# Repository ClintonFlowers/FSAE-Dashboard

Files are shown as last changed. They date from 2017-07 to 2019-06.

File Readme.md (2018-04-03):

# KSU Motorsports Dashboard & Data Logger

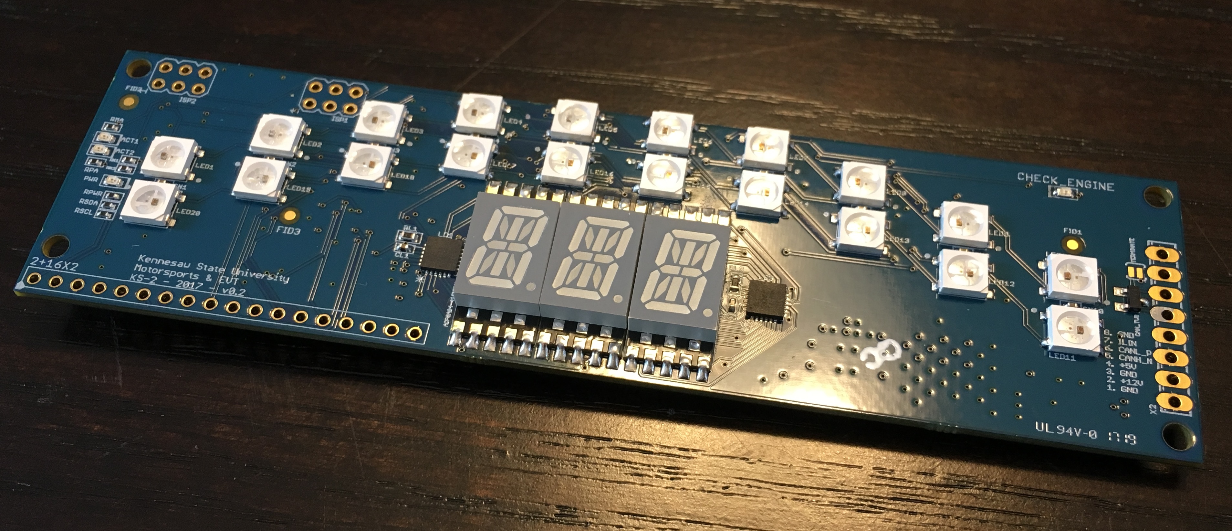
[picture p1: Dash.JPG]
KS-2 Dashboard


This is a custom dashboard / shift-light module created for the Kennesaw State University Motorsports student-built race car, the KS-2.
In a 5" x 1.25" x 0.5" footprint, it has:

* 20 individually-addressable RGB LED's (Neopixels)
* 3 14-segment alphanumeric LED elements for string output via scrolling text
* CAN bus communication with solderable termination jumper
* Onboard 12V to 5V switching converter plus overvoltage, transient, overcurrent, and reverse-voltage protection (i.e., Partially Student Resistant)
* A 9-DOF (accelerometer/gyro/magnetometer) inertial measurement unit with integrated sensor fusion
* A battery-backed Realtime Clock
* A Micro SD Card slot
* A 5-way Tactile Switch/Joystick
* Expansion capability via a 0.1" header at the bottom left, designed for a 16x2 character matrix or any I2C device

It's based on a combination of a Atmega328P (Arduino Uno) and a Atmega2560 (Arduino Mega) to ensure team members can program it into the future.

I've included a PDF to view the schematic without EagleCAD, and the models (STL/SLDPRT) of the enclosure pieces. The version 1 faceplate and backplate were designed for Formlabs clear resin, as the backplate's integrated cable-tie strain-relief loops may break more easily on FDM prints (due to Z-axis layer adhesion). Newer designs (version 2+) use a thin waterjet polycarbonate faceplate for simplicity.

Feel free to contact me with any questions,

Clinton Flowers

clintonflowers222@gmail.com

   Copyright 2017 Clinton Flowers

   Licensed under the Apache License, Version 2.0 (the "License");
   you may not use this file except in compliance with the License.
   You may obtain a copy of the License at

       http://www.apache.org/licenses/LICENSE-2.0

   Unless required by applicable law or agreed to in writing, software
   distributed under the License is distributed on an "AS IS" BASIS,
   WITHOUT WARRANTIES OR CONDITIONS OF ANY KIND, either express or implied.
   See the License for the specific language governing permissions and
   limitations under the License.

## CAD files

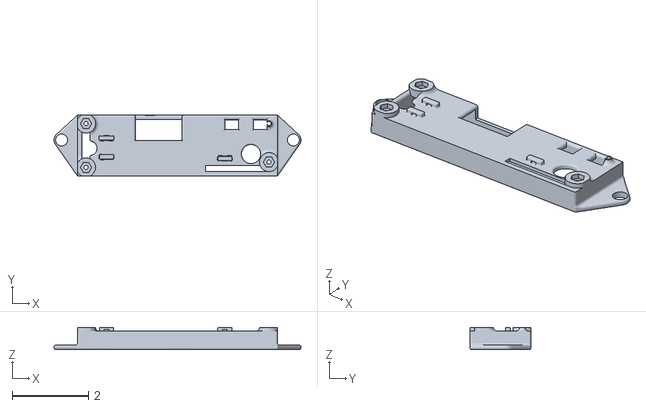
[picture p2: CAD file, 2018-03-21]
Enclosure/Dash v0.2 Backplate Version 2.STL
6.48 x 1.60 x 0.587

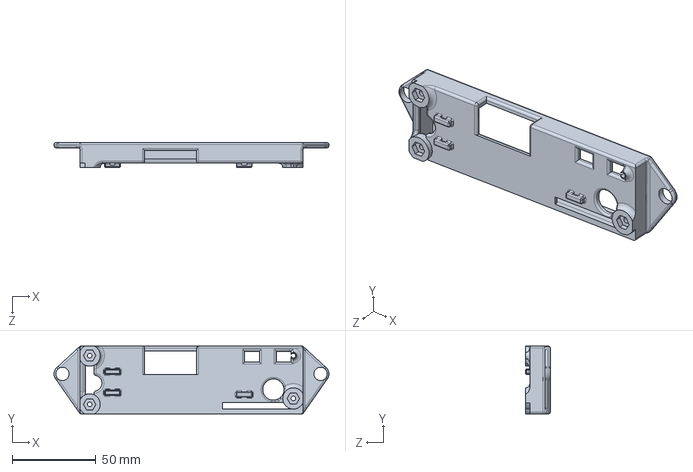
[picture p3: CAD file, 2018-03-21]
Enclosure/Dash Faceplate Version 2.SLDPRT
164.6 x 40.6 x 14.9 mm

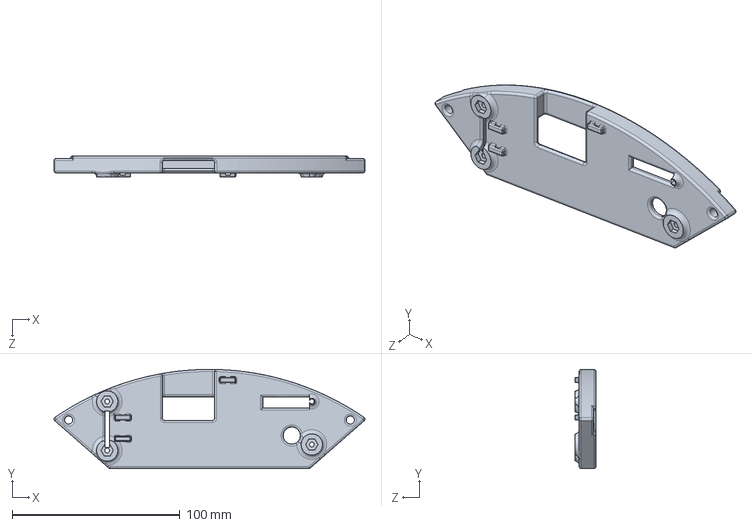
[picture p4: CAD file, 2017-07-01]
Enclosure/Dash Backplate.SLDPRT
185.3 x 59.1 x 12.7 mm

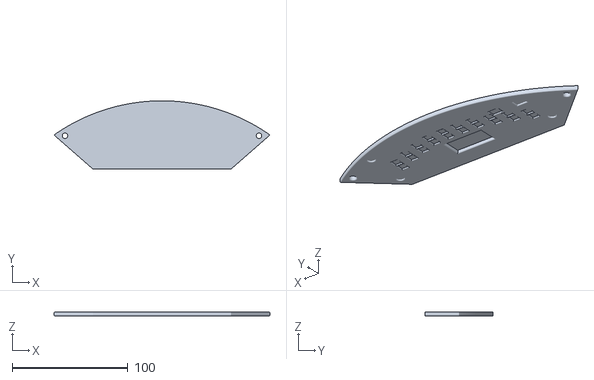
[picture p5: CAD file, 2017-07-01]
Enclosure/Dash v0.2 Faceplate - Formlabs Clear Resin.STL
186.9 x 59.1 x 3.17

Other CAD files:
Enclosure/Dash v0.2 Backplate - Formlabs Clear Resin.STL
Enclosure/Dash Faceplate.SLDPRT

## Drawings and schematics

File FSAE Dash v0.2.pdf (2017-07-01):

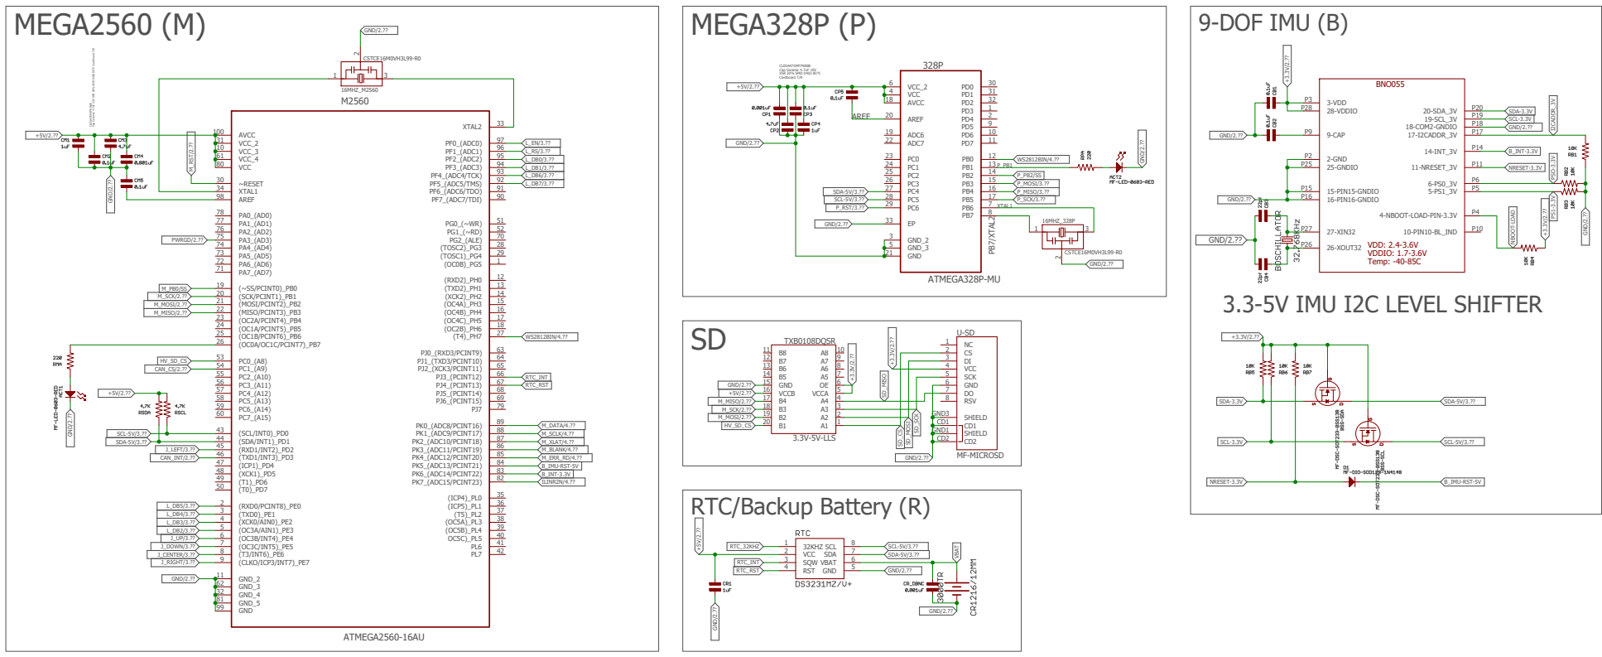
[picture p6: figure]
CL05A475MP7NRB8; 9-DOF IMU (B); 3.3-5V IMU I2C LEVEL SHIFTER; RTC/Backup Battery (R); ATMEGA328P-MU; CSTCE16M0VH3L99-R0; ATMEGA2560-16AU; MF-MICROSD; TXB0108DQSR; MEGA2560 (M); MEGA328P (P); VCC_2 6 VCC 4 AVCC 18; AREF 20; ADC6 19 ADC7 22; GND_2 3 GND_3 5 GND 21; 16MHZ_328P; AVCC 100 VCC_2 31 VCC_3 10 VCC_4 61 VCC 80; ~RESET 30 XTAL1 34 AREF 98; (~SS/PCINT0)_PB0 19 (SCK/PCINT1)_PB1 20 (MOSI/PCINT2)_PB2 21 (MISO/PCINT3)_PB3 22 (OC2A/PCINT4)_PB4 23 (OC1A/PCINT5)_PB5 24 (OC1B/PCINT6)_PB6 25 (OC0A/OC1C/PCINT7)_PB7 26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

Cap Ceramic 4.7uF 10V X5R 20% SMD 0402 85°C Cardboard T/R CL05A475MP7NRB8 Cap Ceramic 4.7uF 10V X5R 20% SMD 0402 85°C Cardboard T/R

# Key: *P* | P_* = ATMega328P *M* | M_* = ATMega2560 C* = Capacitor R* = Resistor (plus arbitrary variants like CP* meaning a capacitor for 328P) *N* | N_* = Neopixel (WS2812B's)

# References: http://www.14core.com/wp-content/uploads/2015/06/ATMEGA-2560-Pin-Out-Diagram.png

# CONTROL

# NOTES:

The original boards were manufactured using MacroFab's standard 4-layer turnkey process.
If needed, my own library has been included.

Objects beginning with "MF" are from the MacroFab Eagle library, available on Github, along with the relevant DRC. MacroFab has a relatively long lead time (~1mo) and occasionally makes mistakes,
so budget in some ChipQuik and don't procrastinate with orders.
MacroFab's system pulls model numbers from the Eagle "value" field,
so if you're not sure what something here is, see if there's not something in it.

Special thanks to SparkFun and Adafruit OSHW designs, on which parts of this are based.

# Also FYI: WS2812B's (the LED's) have an equivalent Moisture Sensitivity Level 6!

Using them in a reflow oven without using desiccants and baking them before use will lead to cracked epoxy lenses! Resoldering them by hand was not fun.
(The next versions will use the newer variants with redundant data lines as an extra precaution.)

# Clinton Flowers, 2017-7-01 clintonflowers222@gmail.com Kennesaw State University Motorsports

A1 1 A2 2 A3 3 A4 4 VCCA 5 OE 6 A5 7 A6 8 A7 9 A8 10 B8 11 B7 12 B6 13 B5 14 GND 15 VCCB 16 B4 17 B3 18 B2 19 B1 20

5V->3.3V

# CAN/POWER

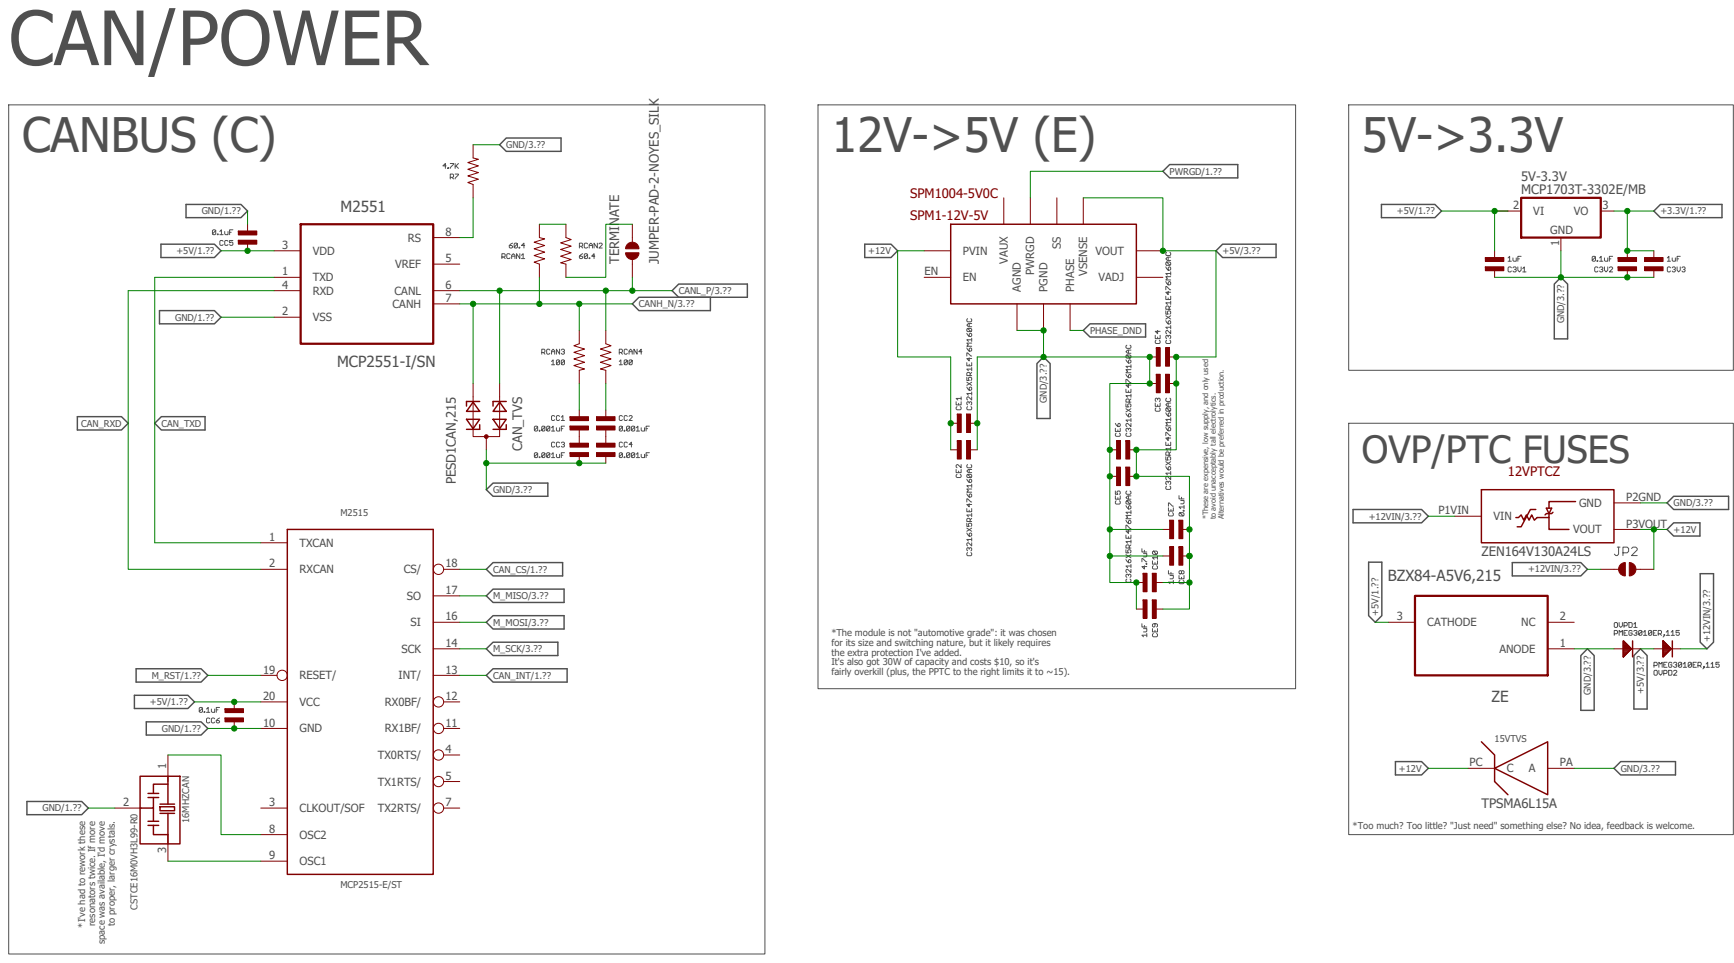
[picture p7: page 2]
TPSMA6L15A; ZEN164V130A24LS; MCP2515-E/ST; MCP2551-I/SN; CSTCE16M0VH3L99-R0; PESD1CAN,215; MCP1703T-3302E/MB; BZX84-A5V6,215; RESET/ 19; SCK; INT/; TX0RTS/; VCC 20; GND 10; TXCAN 1; RXCAN 2; OSC1 9; OSC2 8; CLKOUT/SOF 3; TX1RTS/; TX2RTS/; VDD 3; TXD 1; VSS 2; RXD 4; VREF; CANL; CANH; 16MHZCAN; CAN_TVS; PVIN; VAUX; PWRGD; PGND; PHASE; GND; ANODE; 2 CATHODE 3; VIN P1VIN; P2GND; VOUT; P3VOUT; TERMINATE; 15VTVS; M_MOSI/3.??; CANH_N/3.??; GND/1.??; GND/3.??; CAN_RXD; CAN_TXD; CAN_INT/1.??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

JUMPER-PAD-2-NOYES_SILK CANBUS (C) 12V->5V (E)

VSENSE VOUT VADJ AGND

*These are expensive, low supply, and only used

Alternatives would be preferred in production.

to avoid unacceptably tall electrolytics.

OVP/PTC FUSES

*The module is not "automotive grade": it was chosen
for its size and switching nature, but it likely requires
the extra protection I've added.
It's also got 30W of capacity and costs $10, so it's
fairly overkill (plus, the PPTC to the right limits it to ~15).

*I've had to rework these

resonators twice. If more

space was available, I'd move

to proper, larger crystals.

*Too much? Too little? "Just need" something else? No idea, feedback is welcome.

# ICSP's

# INPUTS/PINOUTS/HEADERS

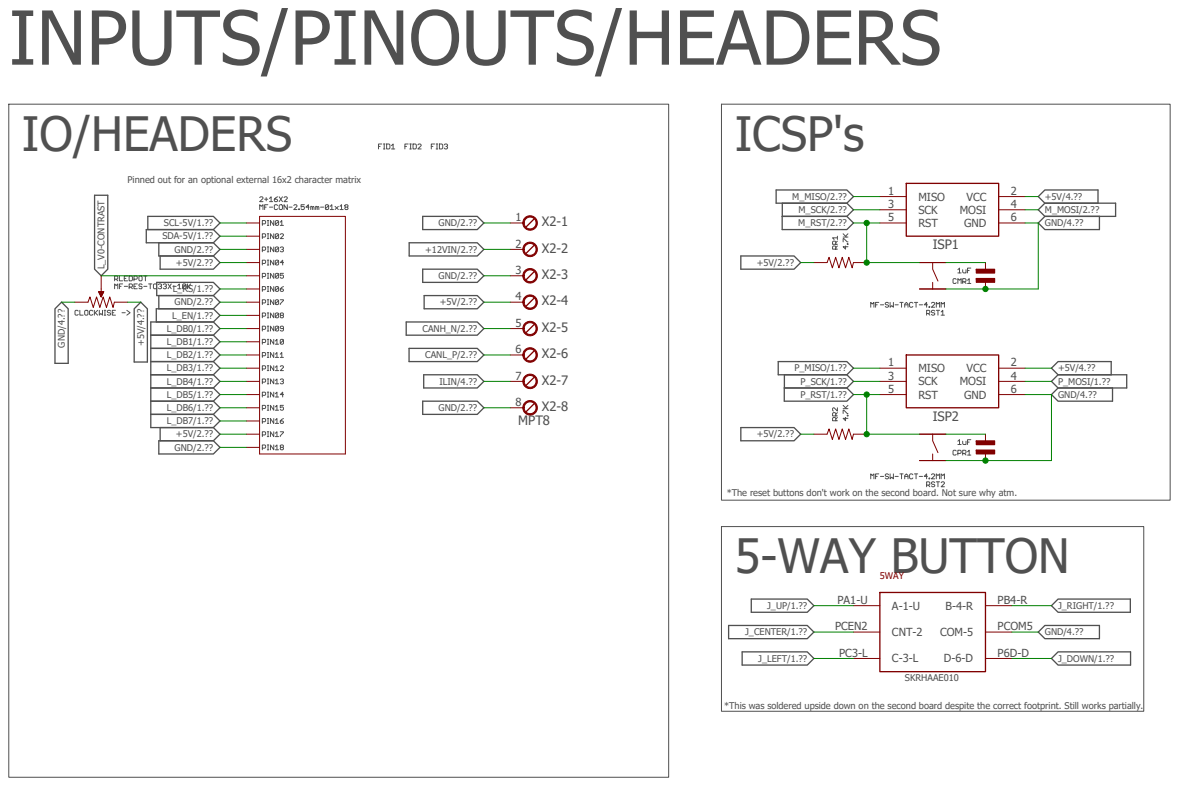
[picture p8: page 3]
5-WAY BUTTON; SKRHAAE010; MPT8; IO/HEADERS; ISP1; MISO 1 SCK 3; RST 5; GND; 6 MOSI; 4 VCC; ISP2; CNT-2 PCEN2; COM-5; PCOM5; +5V/4.?? CANH_N/2.??; GND/2.??; GND/4.??; CANL_P/2.??; ILIN/4.??; P_RST/1.??; M_MOSI/2.??; M_MISO/2.?? M_SCK/2.?? M_RST/2.??; P_SCK/1.??; P_MISO/1.??; P_MOSI/1.??; J_LEFT/1.??; J_DOWN/1.??; J_RIGHT/1.??; J_CENTER/1.??; L_V0-CONTRAST; SCL-5V/1.?? SDA-5V/1.??; +12VIN/2.??; 5WAY

Pinned out for an optional external 16x2 character matrix

*The reset buttons don't work on the second board. Not sure why atm.

*This was soldered upside down on the second board despite the correct footprint. Still works partially.

ALPHANUMERICS (L) | IDIOT LIGHT | POWER LED
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

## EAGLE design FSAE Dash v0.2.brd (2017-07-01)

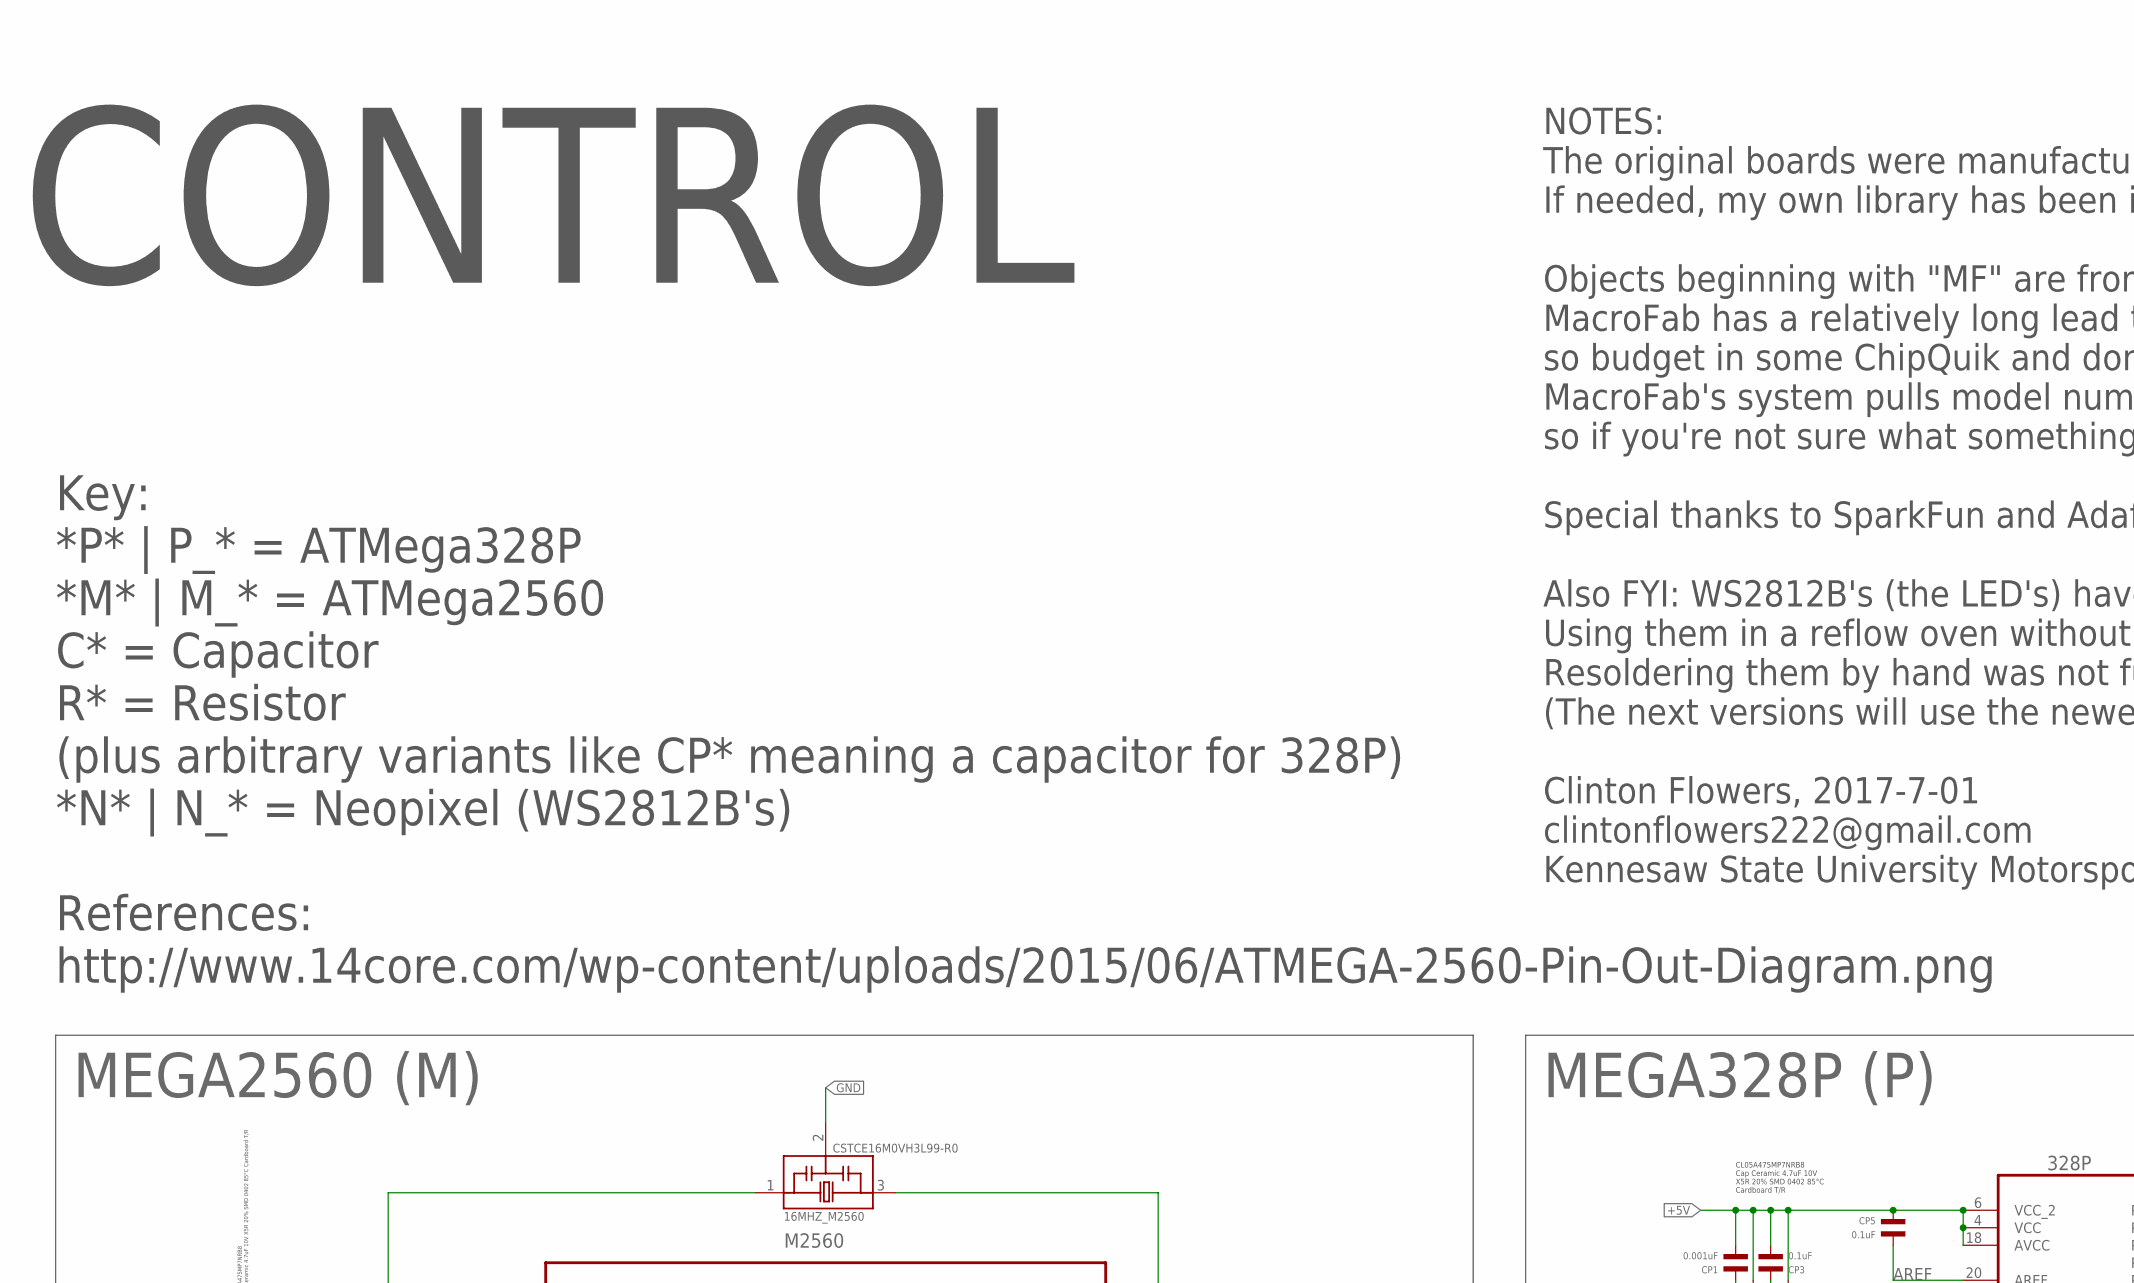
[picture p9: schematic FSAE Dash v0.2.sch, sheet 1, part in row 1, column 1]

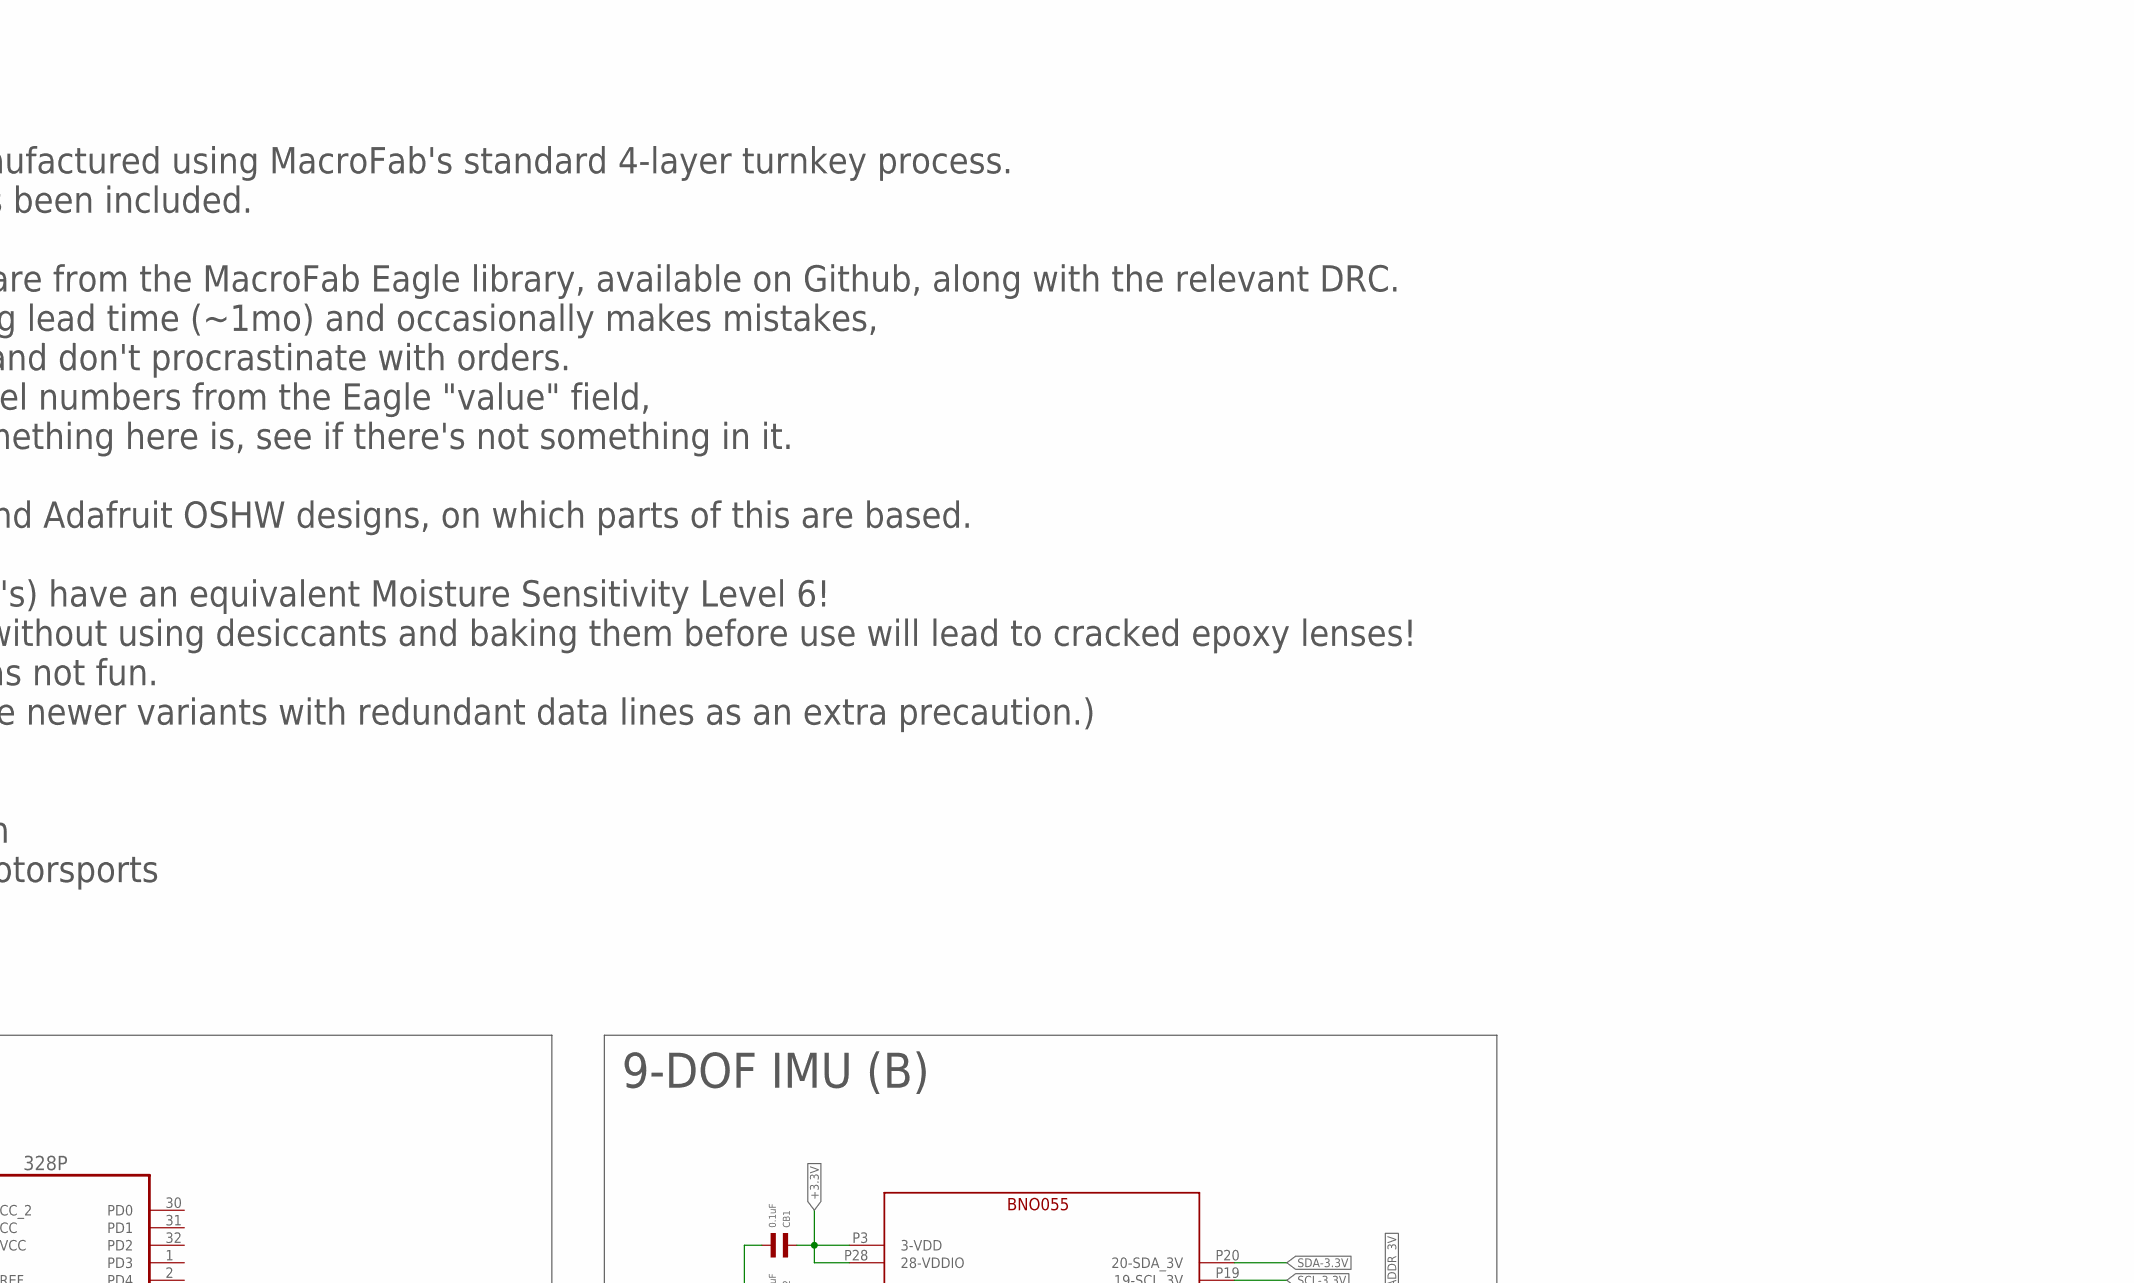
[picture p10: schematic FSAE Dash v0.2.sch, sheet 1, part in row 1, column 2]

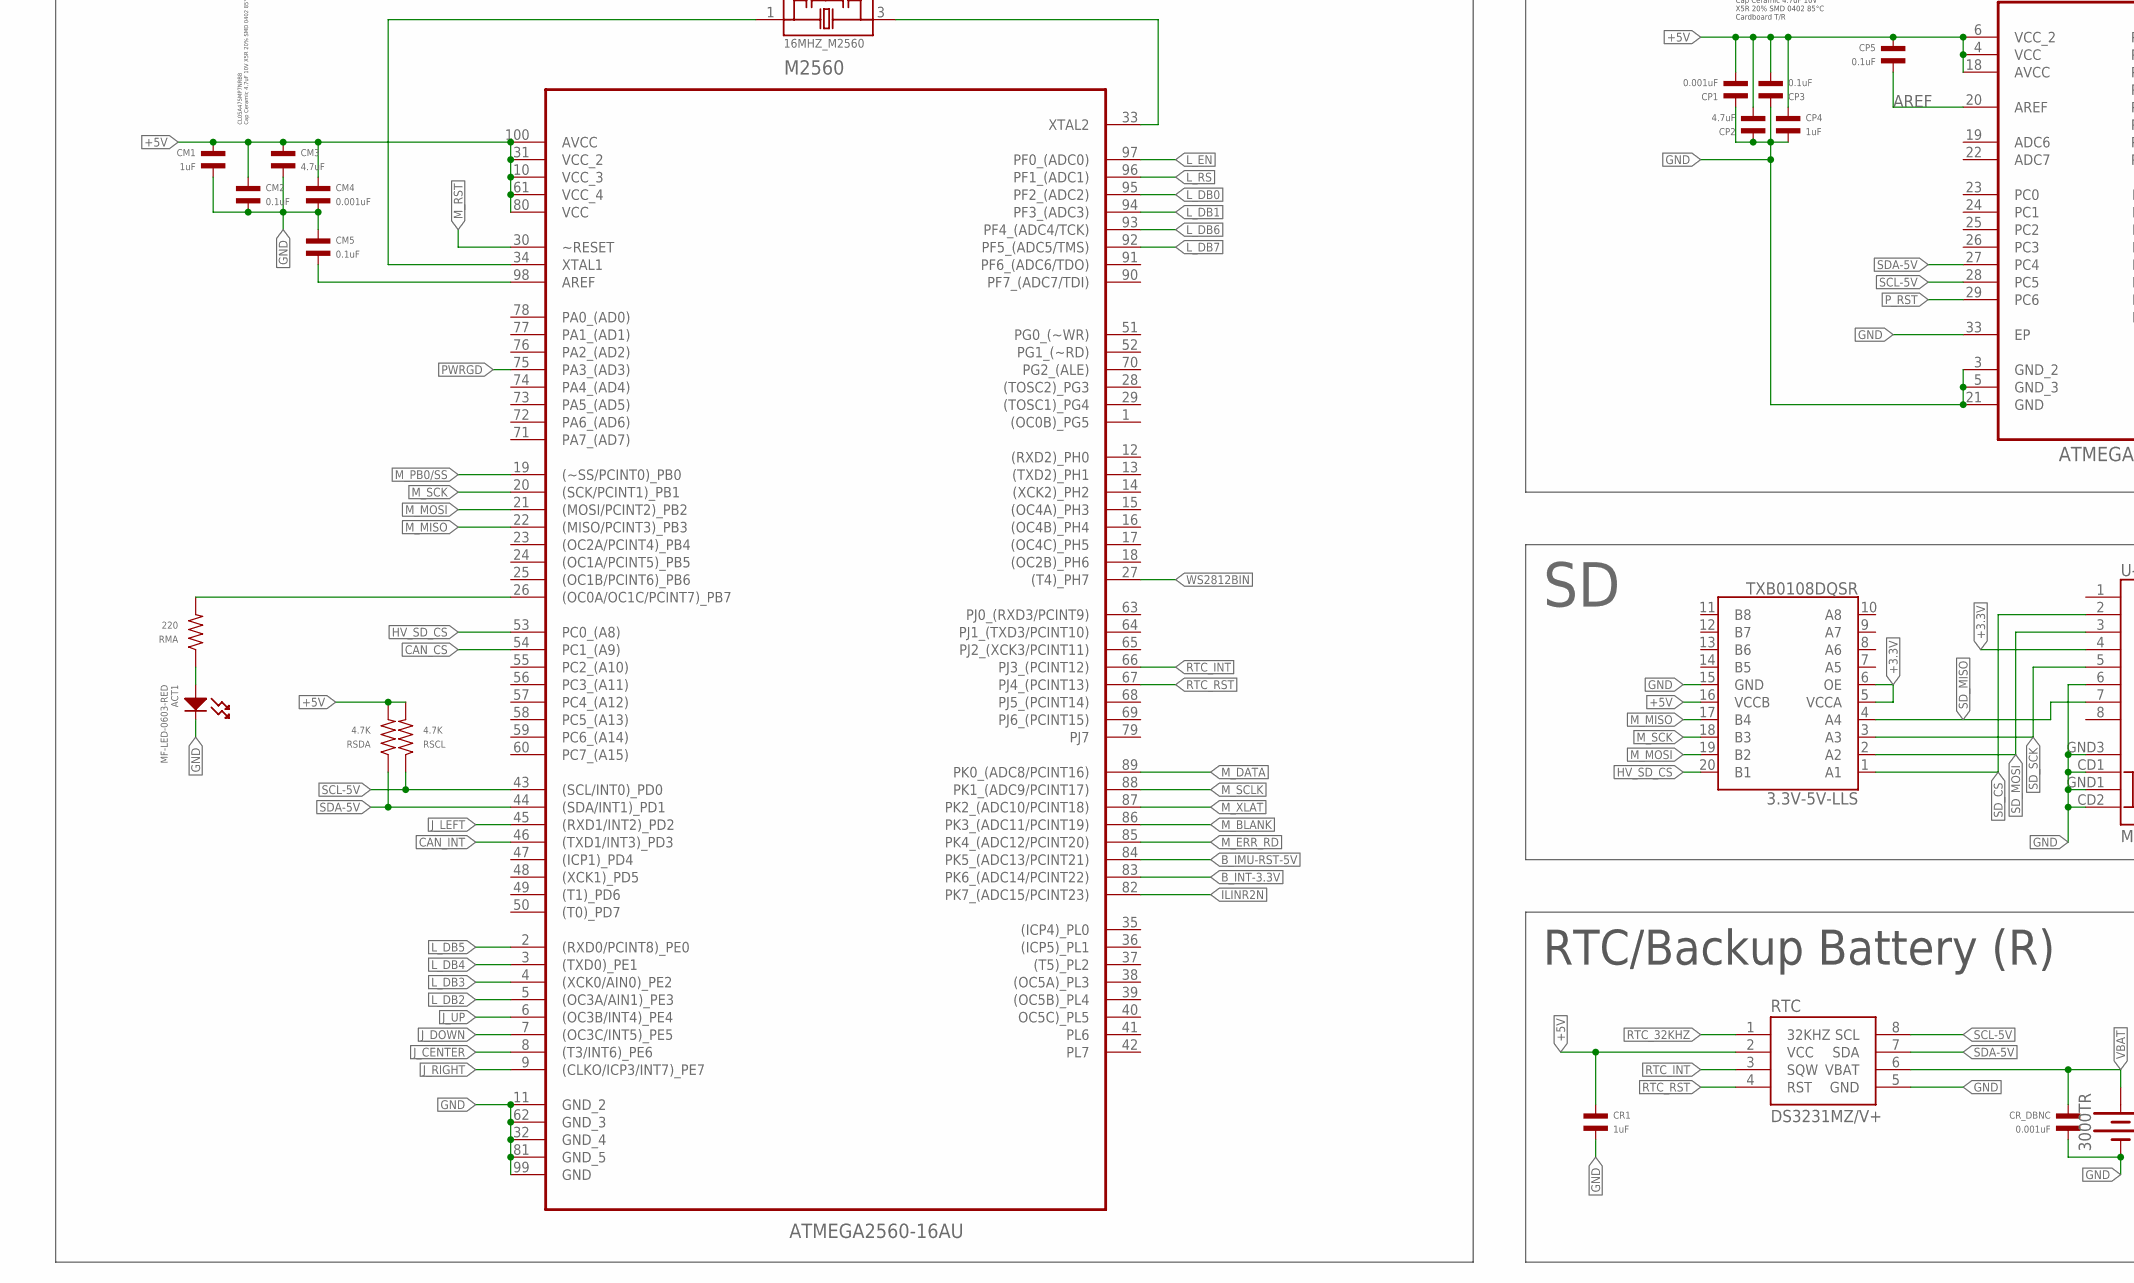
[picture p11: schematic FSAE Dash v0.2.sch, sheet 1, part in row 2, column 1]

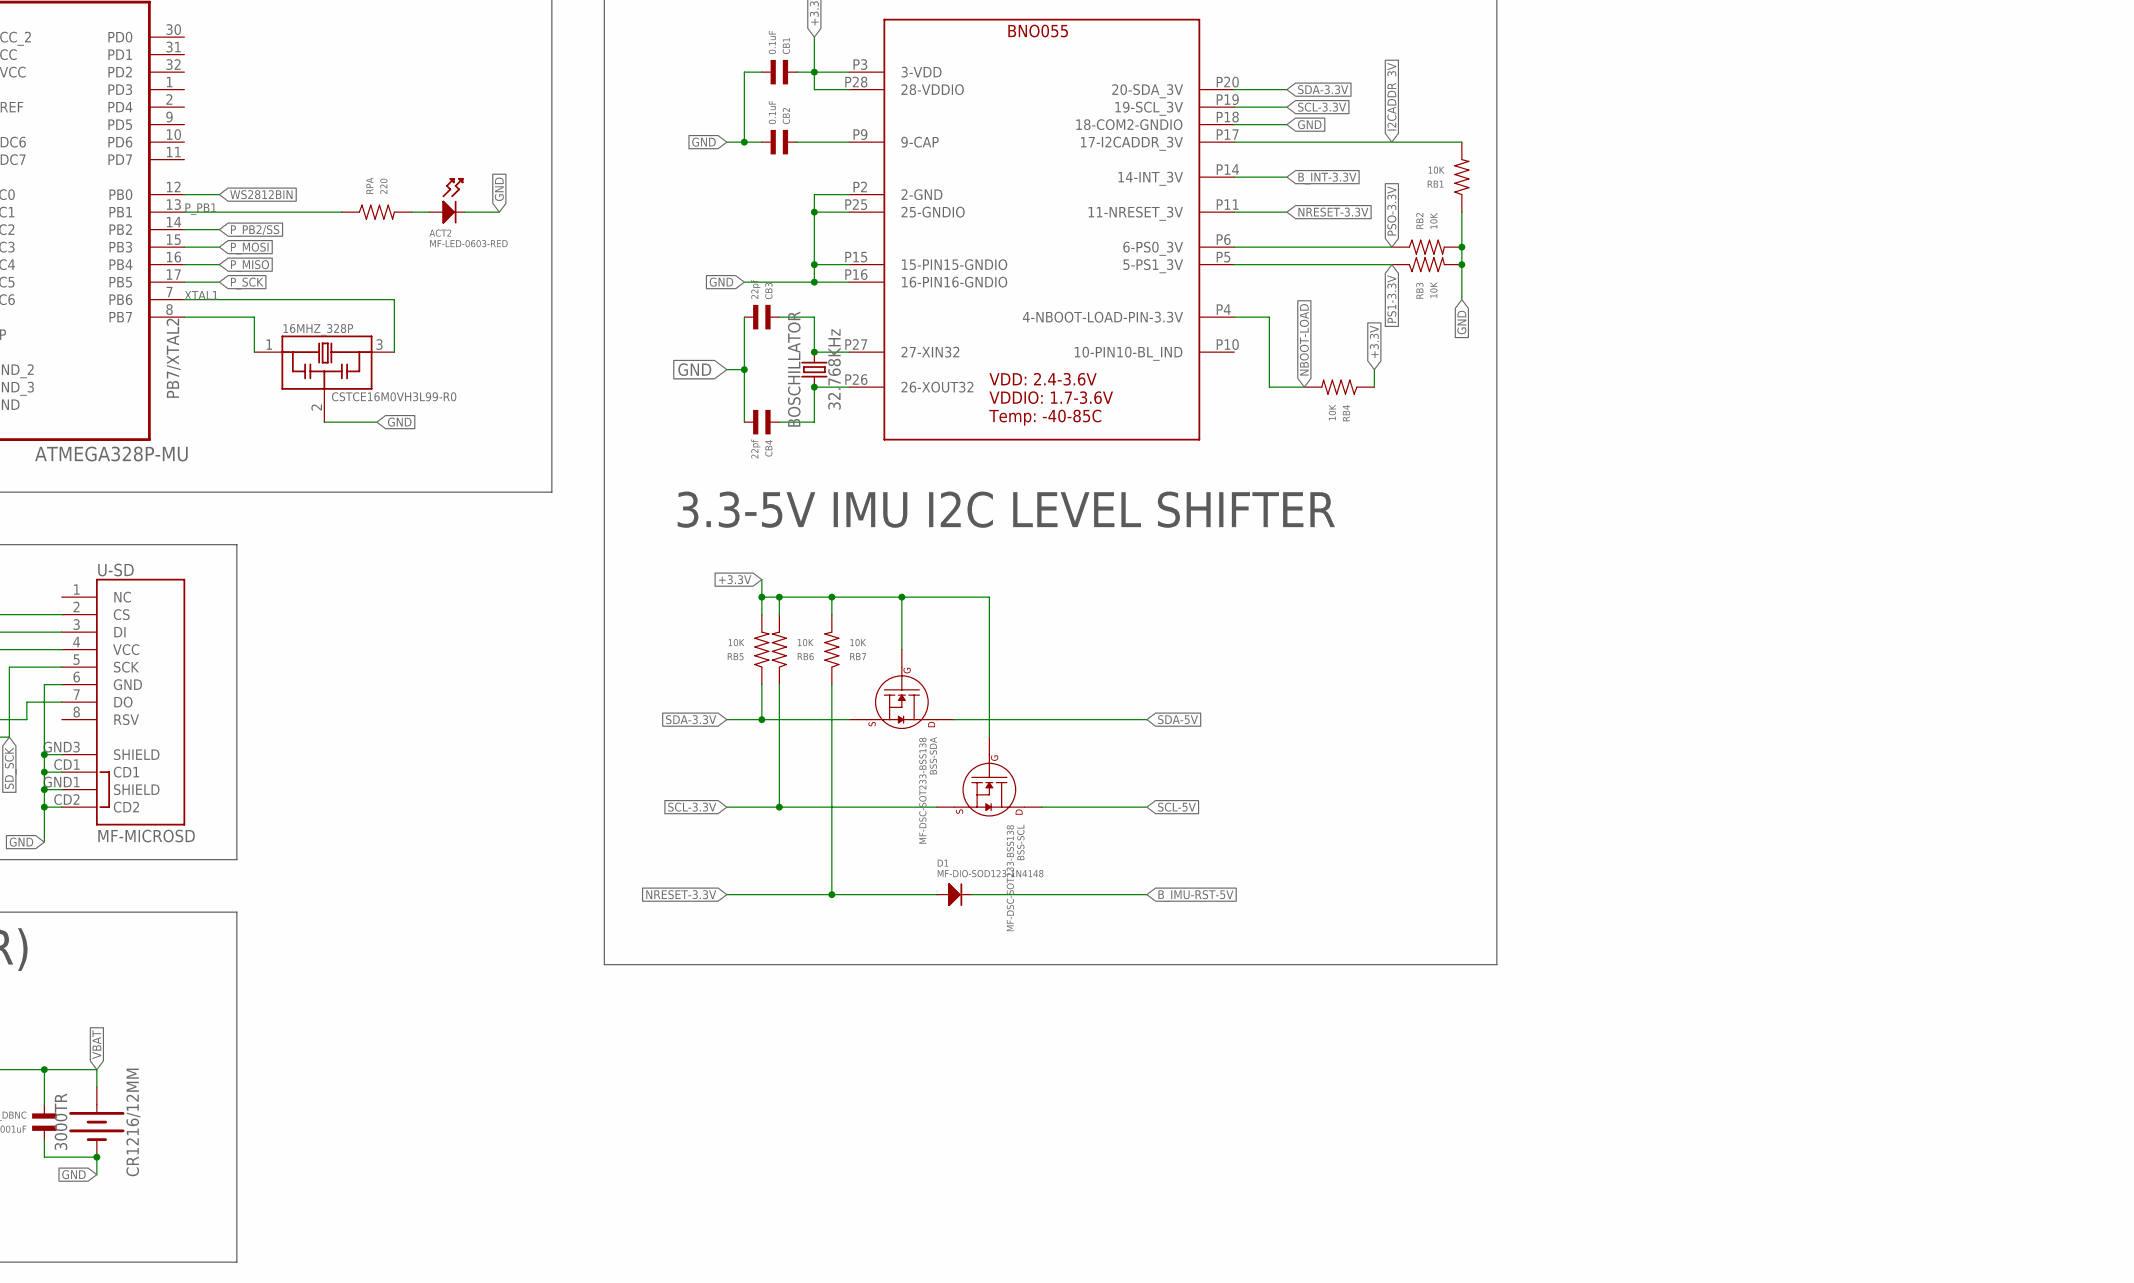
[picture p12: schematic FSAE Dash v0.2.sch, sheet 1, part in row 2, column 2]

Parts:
3.3V-5V-LLS: TXB0108DQSR; UFDFN-20
16MHZ_328P, 16MHZ_M2560: CSTCE16M0VH3L99-R0; OSC_CSTCE16M0V53-R0
328P: ATMEGA328P-MU; QFN50P500X500X100-33N
ACT1, ACT2: MF-LED-0603-RED; LED0603
BNO: BNO055; BOSCH-BNO055
BOSCHILLATOR: 32.768KHz; CRYSTAL-SMD-3.2X1.5MM
BSS-SCL: MF-DSC-SOT233-BSS138; SOT-23-3
BSS-SDA: MF-DSC-SOT233-BSS138; SOT-23-3
CB1, CB2: 0.1uF; C0402
CB3, CB4: 22pf; C0402
CM1: 1uF; C0402
CM2, CM5: 0.1uF; C0402
CM3: 4.7uF; C0402
CM4: 0.001uF; C0402
CP1: 0.001uF; C0402
CP2: 4.7uF; C0402
CP3, CP5: 0.1uF; C0402
CP4: 1uF; C0402
CR1: 1uF; C0402
CR1216/12MM: 3000TR; BATTCON_12MM
CR_DBNC: 0.001uF; C0402
D1: MF-DIO-SOD123-1N4148; SOD-123
M2560: ATMEGA2560-16AU; QFP50P1600X1600X120-100N
RB1, RB2, RB3, RB4, RB5, RB6, RB7: 10K; R0402
RMA: 220; R0402
RPA: 220; R0402
RSCL: 4.7K; R0402
RSDA: 4.7K; R0402
RTC: DS3231MZ/V+; SO08
U-SD: MF-MICROSD; MICROSD_1:1

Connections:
+3.3V: 3.3V-5V-LLS.5 (VCCA), 3.3V-5V-LLS.6 (OE), BNO.P3 (3-VDD), BNO.P28 (28-VDDIO), BSS-SCL.P$1 (GATE), BSS-SDA.P$1 (GATE), CB1.P$1, RB4.P$1, RB5.P$2, RB6.P$2, RB7.P$2, U-SD.4 (VCC); also elsewhere on the board
+5V: 3.3V-5V-LLS.16 (VCCB), 328P.4 (VCC), 328P.6 (VCC_2), 328P.18 (AVCC), CM1.P$1, CM2.P$1, CM3.P$1, CM4.P$1, CP1.P$2, CP2.P$2, CP3.P$2, CP4.P$1, CP5.P$1, CR1.P$1, M2560.10 (VCC_3), M2560.31 (VCC_2), M2560.61 (VCC_4), M2560.80 (VCC), M2560.100 (AVCC), RSCL.P$2, RSDA.P$2, RTC.2 (VCC); also elsewhere on the board
AREF: 328P.20 (AREF), CP5.P$2
BCAP: BNO.P9 (9-CAP), CB2.P$1
B_IMU-RST-5V: D1.CATHODE, M2560.84 (PK5_(ADC13/PCINT21))
B_INT-3.3V: BNO.P14 (14-INT_3V), M2560.83 (PK6_(ADC14/PCINT22))
CAN_CS: M2560.54 (PC1_(A9)); also elsewhere on the board
CAN_INT: M2560.46 ((TXD1/INT3)_PD3); also elsewhere on the board
GND: 3.3V-5V-LLS.15 (GND), 16MHZ_328P.2, 16MHZ_M2560.2, 328P.3 (GND_2), 328P.5 (GND_3), 328P.21 (GND), 328P.33 (EP), ACT1.CATHODE, ACT2.CATHODE, BNO.P2 (2-GND), BNO.P15 (15-PIN15-GNDIO), BNO.P16 (16-PIN16-GNDIO), BNO.P18 (18-COM2-GNDIO), BNO.P25 (25-GNDIO), CB1.P$2, CB2.P$2, CB3.P$2, CB4.P$2, CM1.P$2, CM2.P$2, CM3.P$2, CM4.P$2, CM5.P$1, CP1.P$1, CP2.P$1, CP3.P$1, CP4.P$2, CR1.P$2, CR1216/12MM.GND (-), CR_DBNC.P$2, M2560.11 (GND_2), M2560.32 (GND_4), M2560.62 (GND_3), M2560.81 (GND_5), M2560.99 (GND), RB1.P$1, RB2.P$2, RB3.P$2, RTC.5 (GND), U-SD.6 (GND), U-SD.CD1, U-SD.CD2, U-SD.GND1 (SHIELD), U-SD.GND3 (SHIELD); also elsewhere on the board
HV_SD_CS: 3.3V-5V-LLS.20 (B1), M2560.53 (PC0_(A8))
I2CADDR_3V: BNO.P17 (17-I2CADDR_3V), RB1.P$2
ILINR2N: M2560.82 (PK7_(ADC15/PCINT23)); also elsewhere on the board
J_CENTER: M2560.8 ((T3/INT6)_PE6); also elsewhere on the board
J_DOWN: M2560.7 ((OC3C/INT5)_PE5); also elsewhere on the board
J_LEFT: M2560.45 ((RXD1/INT2)_PD2); also elsewhere on the board
J_RIGHT: M2560.9 ((CLKO/ICP3/INT7)_PE7); also elsewhere on the board
J_UP: M2560.6 ((OC3B/INT4)_PE4); also elsewhere on the board
L_DB0: M2560.95 (PF2_(ADC2)); also elsewhere on the board
L_DB1: M2560.94 (PF3_(ADC3)); also elsewhere on the board
L_DB2: M2560.5 ((OC3A/AIN1)_PE3); also elsewhere on the board
L_DB3: M2560.4 ((XCK0/AIN0)_PE2); also elsewhere on the board
L_DB4: M2560.3 ((TXD0)_PE1); also elsewhere on the board
L_DB5: M2560.2 ((RXD0/PCINT8)_PE0); also elsewhere on the board
L_DB6: M2560.93 (PF4_(ADC4/TCK)); also elsewhere on the board
L_DB7: M2560.92 (PF5_(ADC5/TMS)); also elsewhere on the board
L_EN: M2560.97 (PF0_(ADC0)); also elsewhere on the board
L_RS: M2560.96 (PF1_(ADC1)); also elsewhere on the board
M_BLANK: M2560.86 (PK3_(ADC11/PCINT19)); also elsewhere on the board
M_DATA: M2560.89 (PK0_(ADC8/PCINT16)); also elsewhere on the board
M_ERR_RD: M2560.85 (PK4_(ADC12/PCINT20)); also elsewhere on the board
M_MISO: 3.3V-5V-LLS.17 (B4), M2560.22 ((MISO/PCINT3)_PB3); also elsewhere on the board
M_MOSI: 3.3V-5V-LLS.19 (B2), M2560.21 ((MOSI/PCINT2)_PB2); also elsewhere on the board
M_PB0/SS: M2560.19 ((~SS/PCINT0)_PB0)
M_RST: M2560.30 (~RESET); also elsewhere on the board
M_SCK: 3.3V-5V-LLS.18 (B3), M2560.20 ((SCK/PCINT1)_PB1); also elsewhere on the board
M_SCLK: M2560.88 (PK1_(ADC9/PCINT17)); also elsewhere on the board
M_XLAT: M2560.87 (PK2_(ADC10/PCINT18)); also elsewhere on the board
unnamed: ACT2.ANODE, RPA.P$2
unnamed: 16MHZ_M2560.3, M2560.33 (XTAL2)
unnamed: CM5.P$2, M2560.98 (AREF)
unnamed: 16MHZ_M2560.1, M2560.34 (XTAL1)
unnamed: ACT1.ANODE, RMA.P$1
unnamed: BNO.P26 (26-XOUT32), BOSCHILLATOR.P$1 (1), CB4.P$1
unnamed: BNO.P27 (27-XIN32), BOSCHILLATOR.P$2 (2), CB3.P$1
unnamed: M2560.26 ((OC0A/OC1C/PCINT7)_PB7), RMA.P$2
NBOOT-LOAD: BNO.P4 (4-NBOOT-LOAD-PIN-3.3V), RB4.P$2
NRESET-3.3V: BNO.P11 (11-NRESET_3V), D1.ANODE, RB7.P$1
PB7/XTAL2: 16MHZ_328P.1, 328P.8 (PB7)
PS1-3.3V: BNO.P5 (5-PS1_3V), RB3.P$1
PSO-3.3V: BNO.P6 (6-PS0_3V), RB2.P$1
PWRGD: M2560.75 (PA3_(AD3)); also elsewhere on the board
P_MISO: 328P.16 (PB4); also elsewhere on the board
P_MOSI: 328P.15 (PB3); also elsewhere on the board
P_PB1: 328P.13 (PB1), RPA.P$1
P_PB2/SS: 328P.14 (PB2)
P_RST: 328P.29 (PC6); also elsewhere on the board
P_SCK: 328P.17 (PB5); also elsewhere on the board
RTC_32KHZ: RTC.1 (32KHZ)
RTC_INT: M2560.66 (PJ3_(PCINT12)), RTC.3 (SQW)
RTC_RST: M2560.67 (PJ4_(PCINT13)), RTC.4 (RST)
SCL-3.3V: BNO.P19 (19-SCL_3V), BSS-SCL.P$2 (SOURCE), RB6.P$1
SCL-5V: 328P.28 (PC5), BSS-SCL.P$3 (DRAIN), M2560.43 ((SCL/INT0)_PD0), RSCL.P$1, RTC.8 (SCL); also elsewhere on the board
SDA-3.3V: BNO.P20 (20-SDA_3V), BSS-SDA.P$2 (SOURCE), RB5.P$1
SDA-5V: 328P.27 (PC4), BSS-SDA.P$3 (DRAIN), M2560.44 ((SDA/INT1)_PD1), RSDA.P$1, RTC.7 (SDA); also elsewhere on the board
SD_CS: 3.3V-5V-LLS.1 (A1), U-SD.2 (CS)
SD_MISO: 3.3V-5V-LLS.4 (A4), U-SD.7 (DO)
SD_MOSI: 3.3V-5V-LLS.2 (A2), U-SD.3 (DI)
SD_SCK: 3.3V-5V-LLS.3 (A3), U-SD.5 (SCK)
VBAT: CR1216/12MM.PWR@1 (+), CR_DBNC.P$1, RTC.6 (VBAT)
WS2812BIN: 328P.12 (PB0), M2560.27 ((T4)_PH7); also elsewhere on the board
XTAL1: 16MHZ_328P.3, 328P.7 (PB6)

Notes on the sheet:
MEGA2560 (M)
MEGA328P (P)
CL05A475MP7NRB8 Cap Ceramic 4.7uF 10V X5R 20% SMD 0402 85°C Cardboard T/R
CL05A475MP7NRB8 Cap Ceramic 4.7uF 10V X5R 20% SMD 0402 85°C Cardboard T/R
Key: *P* | P_* = ATMega328P *M* | M_* = ATMega2560 C* = Capacitor R* = Resistor (plus arbitrary variants like CP* meaning a capacitor for 328P) *N* | N_* = Neopixel (WS2812B's) References: http://www.14core.com/wp-content/uploads/2015/06/ATMEGA-2560-Pin-Out-Diagram.png
CONTROL
9-DOF IMU (B)
3.3-5V IMU I2C LEVEL SHIFTER
RTC/Backup Battery (R)
NOTES: The original boards were manufactured using MacroFab's standard 4-layer turnkey process. If needed, my own library has been included. Objects beginning with "MF" are from the MacroFab Eagle library, available on Github, along with the relevant DRC. MacroFab has a relatively long lead time (~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

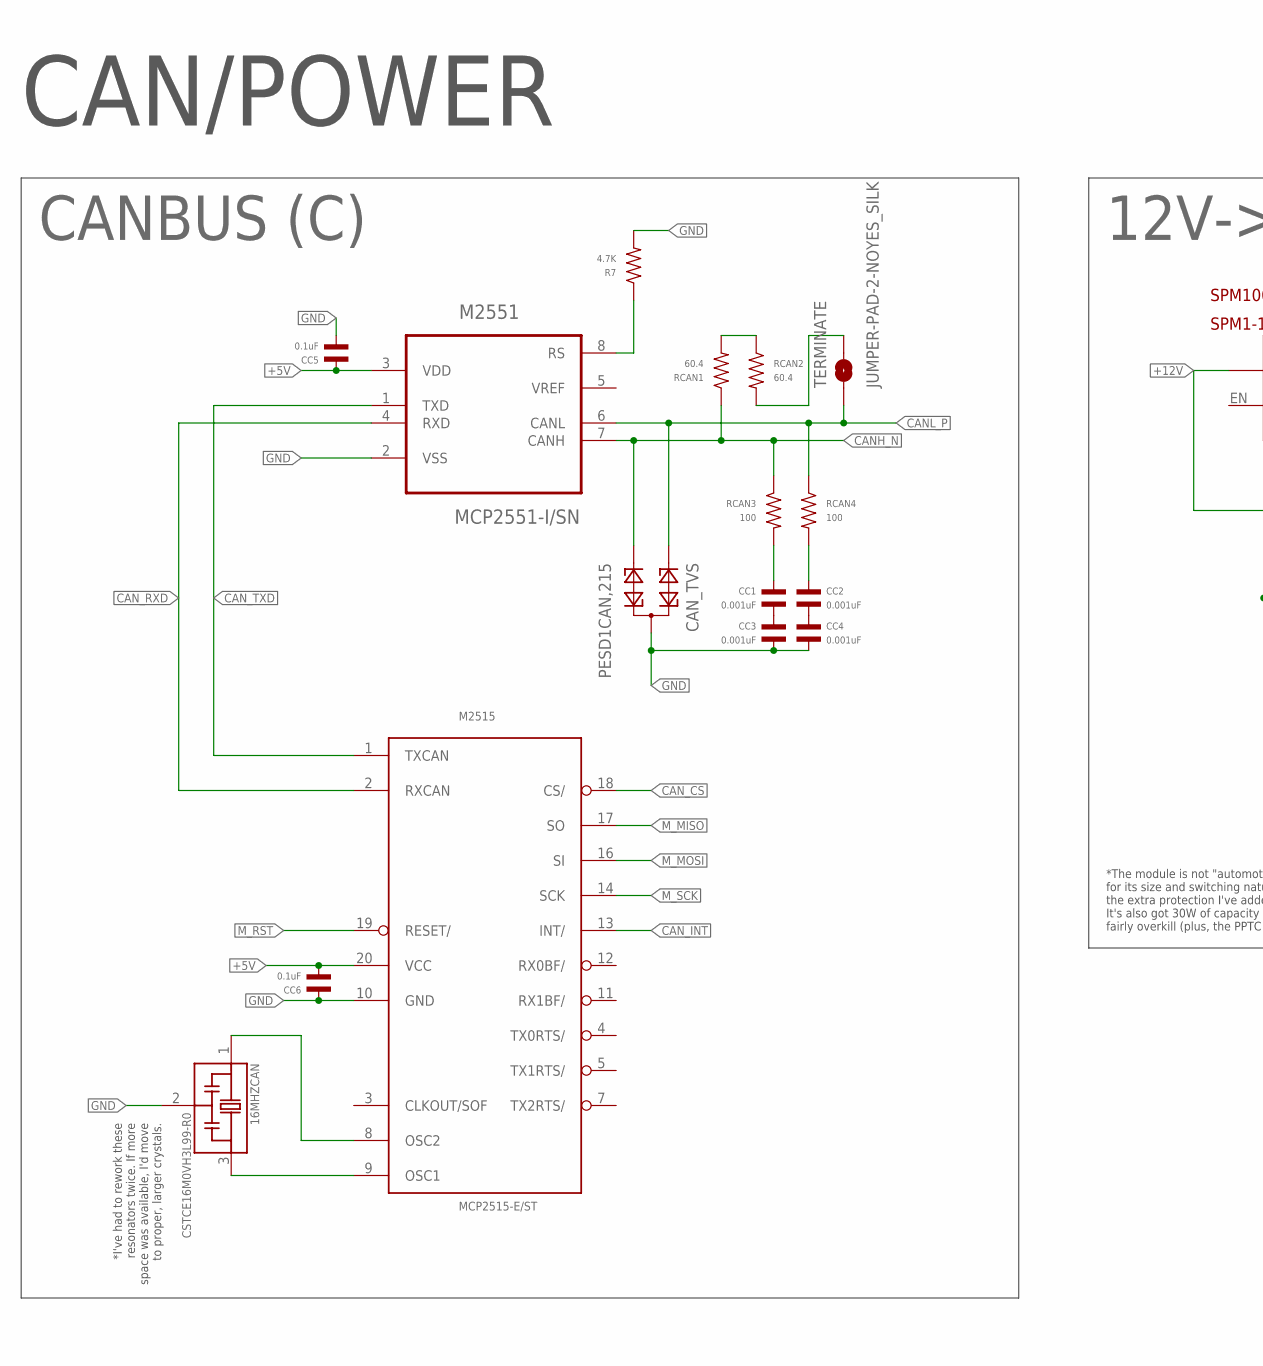
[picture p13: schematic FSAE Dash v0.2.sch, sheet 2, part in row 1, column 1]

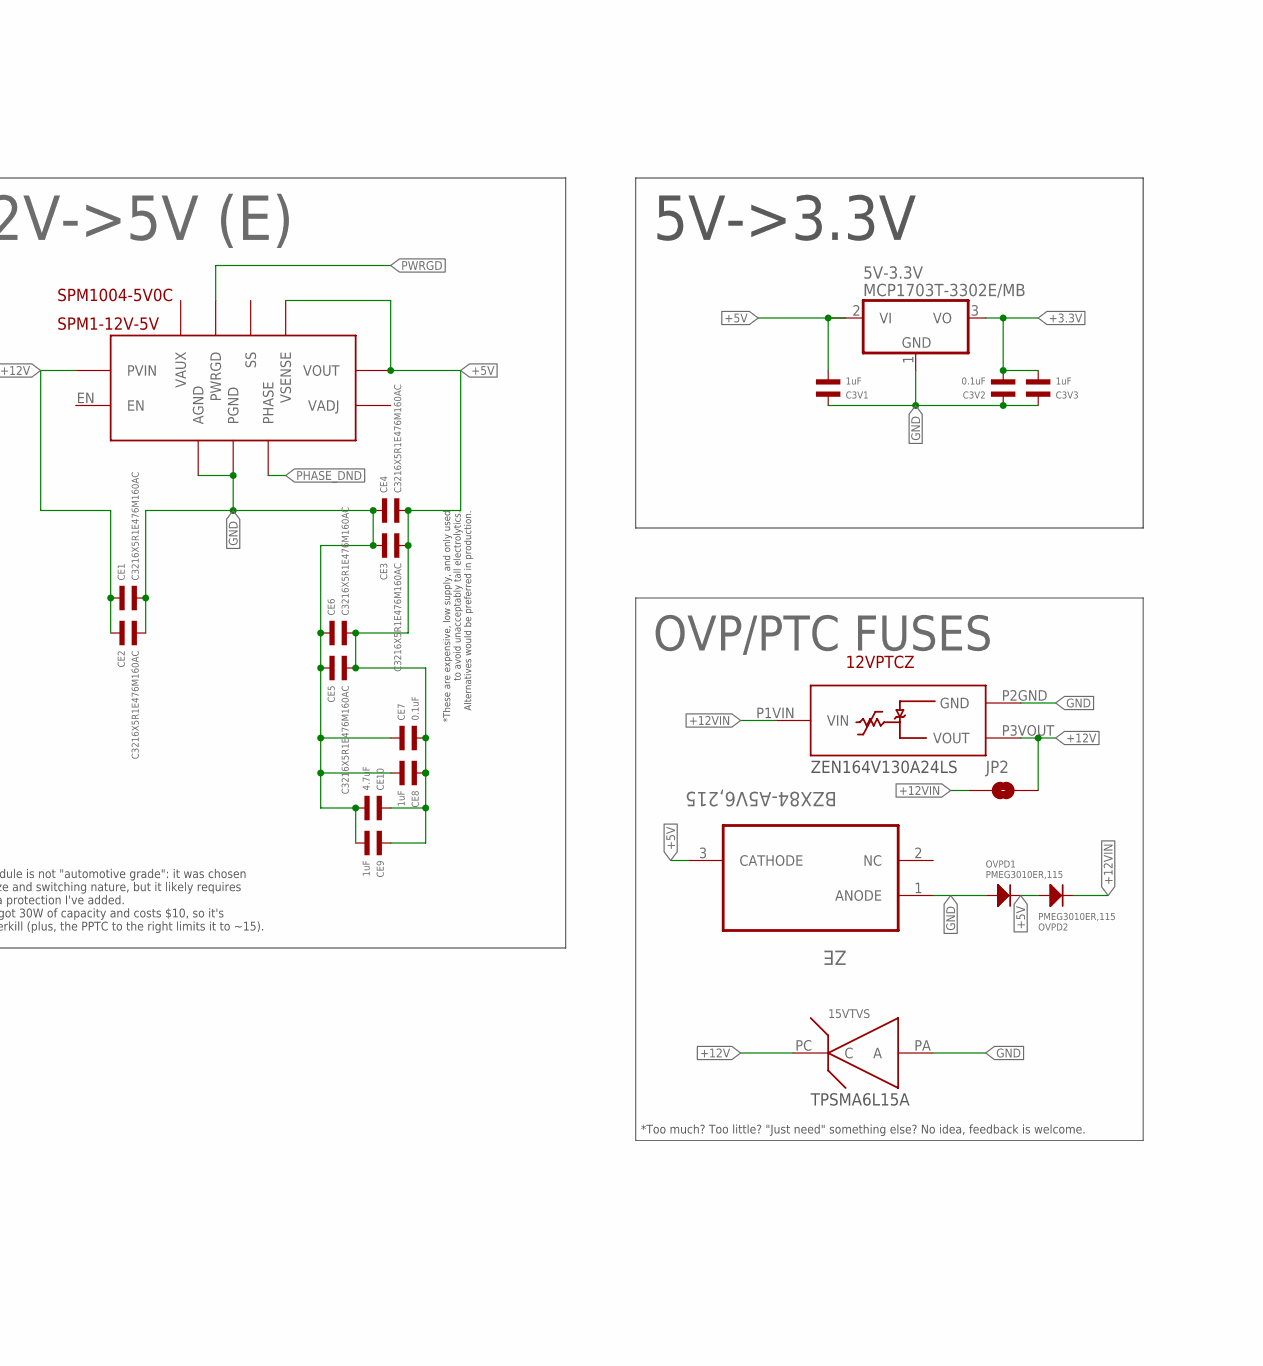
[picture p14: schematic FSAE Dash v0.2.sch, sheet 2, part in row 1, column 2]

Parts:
5V-3.3V: MCP1703T-3302E/MB; SOT89
12VPTCZ: ZEN164V130A24LS; LITTELFUSE-POLYZEN-ZEN164V130A24LS
15VTVS: TPSMA6L15A; LITTELFUSE-TPSMA6L15A
16MHZCAN: CSTCE16M0VH3L99-R0; OSC_CSTCE16M0V53-R0
C3V1, C3V3: 1uF; C0402
C3V2: 0.1uF; C0402
CAN_TVS: PESD1CAN,215; SOT23
CC1, CC2, CC3, CC4: 0.001uF; C0402
CC5, CC6: 0.1uF; C0402
CE1, CE2, CE3, CE4, CE5, CE6: C3216X5R1E476M160AC; C1206
CE7: 0.1uF; C0402
CE8, CE9: 1uF; C0402
CE10: 4.7uF; C0402
JP2: JUMPER-SMT_2_NO_SILK; SMT-JUMPER_2_NO_SILK
M2515: MCP2515-E/ST; TSSOP20
M2551: MCP2551-I/SN; SOIC127P600X175-8N
OVPD1, OVPD2: PMEG3010ER,115; SOD-123
R7: 4.7K; R0402
RCAN1, RCAN2: 60.4; R0402
RCAN3, RCAN4: 100; R0402
SPM1-12V-5V: SPM1004-5V0C
TERMINATE: JUMPER-PAD-2-NOYES_SILK; PAD-JUMPER-2-NO_YES_SILK
ZE: BZX84-A5V6,215; SOT91P240X110-3N

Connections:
+3.3V: 5V-3.3V.3 (VO), C3V2.P$2, C3V3.P$2; also elsewhere on the board
+5V: 5V-3.3V.2 (VI), 5V-3.3V.2@1 (VI1), C3V1.P$2, CC5.P$1, CC6.P$2, CE3.P$2, CE4.P$2, CE5.P$2, CE6.P$2, CE7.P$2, CE8.P$1, CE9.P$1, CE10.P$1, M2515.20 (VCC), M2551.3 (VDD), OVPD1.CATHODE, OVPD2.ANODE, SPM1-12V-5V.VOUT$1 (VOUT), SPM1-12V-5V.VOUT$2 (VOUT), SPM1-12V-5V.VOUT$3 (VOUT), SPM1-12V-5V.VOUT$4 (VOUT), SPM1-12V-5V.VOUT$5 (VOUT), SPM1-12V-5V.VOUT$6 (VOUT), SPM1-12V-5V.VOUT$7 (VOUT), SPM1-12V-5V.VOUT$8 (VOUT), SPM1-12V-5V.VOUT$9 (VOUT), SPM1-12V-5V.VOUT$10 (VOUT), SPM1-12V-5V.VOUT$11 (VOUT), SPM1-12V-5V.VOUT$12 (VOUT), SPM1-12V-5V.VOUT$13 (VOUT), SPM1-12V-5V.VOUT$14 (VOUT), SPM1-12V-5V.VOUT$15 (VOUT), SPM1-12V-5V.VOUT$16 (VOUT), SPM1-12V-5V.VOUT$17 (VOUT), SPM1-12V-5V.VOUT$18 (VOUT), SPM1-12V-5V.VSENSE, ZE.3 (CATHODE); also elsewhere on the board
+12V: 12VPTCZ.P3VOUT (VOUT), 15VTVS.PC (C), CE1.P$1, CE2.P$1, JP2.2, SPM1-12V-5V.PVIN$1 (PVIN), SPM1-12V-5V.PVIN$2 (PVIN), SPM1-12V-5V.PVIN$3 (PVIN), SPM1-12V-5V.PVIN$4 (PVIN), SPM1-12V-5V.PVIN$5 (PVIN), SPM1-12V-5V.PVIN$6 (PVIN), SPM1-12V-5V.PVIN$7 (PVIN), SPM1-12V-5V.PVIN$8 (PVIN)
+12VIN: 12VPTCZ.P1VIN (VIN), JP2.1, OVPD2.CATHODE; also elsewhere on the board
CANH_N: CAN_TVS.2, M2551.7 (CANH), RCAN1.P$1, RCAN3.P$1; also elsewhere on the board
CANL_P: CAN_TVS.1, M2551.6 (CANL), RCAN4.P$1, TERMINATE.1; also elsewhere on the board
CAN_CS: M2515.18 (CS/); also elsewhere on the board
CAN_INT: M2515.13 (INT/); also elsewhere on the board
CAN_RXD: M2515.2 (RXCAN), M2551.4 (RXD)
CAN_TXD: M2515.1 (TXCAN), M2551.1 (TXD)
GND: 5V-3.3V.1 (GND), 12VPTCZ.P2GND (GND), 15VTVS.PA (A), 16MHZCAN.2, C3V1.P$1, C3V2.P$1, C3V3.P$1, CAN_TVS.3, CC3.P$2, CC4.P$2, CC5.P$2, CC6.P$1, CE1.P$2, CE2.P$2, CE3.P$1, CE4.P$1, CE5.P$1, CE6.P$1, CE7.P$1, CE8.P$2, CE9.P$2, CE10.P$2, M2515.10 (GND), M2551.2 (VSS), OVPD1.ANODE, R7.P$2, SPM1-12V-5V.AGND$1 (AGND), SPM1-12V-5V.AGND$2 (AGND), SPM1-12V-5V.AGND$3 (AGND), SPM1-12V-5V.PGND$1 (PGND), SPM1-12V-5V.PGND$2 (PGND), SPM1-12V-5V.PGND$3 (PGND), SPM1-12V-5V.PGND$4 (PGND), SPM1-12V-5V.PGND$5 (PGND), SPM1-12V-5V.PGND$6 (PGND), SPM1-12V-5V.PGND$7 (PGND), SPM1-12V-5V.PGND$8 (PGND), SPM1-12V-5V.PGND$9 (PGND), SPM1-12V-5V.PGND$10 (PGND), SPM1-12V-5V.PGND$11 (PGND), SPM1-12V-5V.PGND$12 (PGND), SPM1-12V-5V.PGND$13 (PGND), SPM1-12V-5V.PGND$14 (PGND), SPM1-12V-5V.PGND$15 (PGND), SPM1-12V-5V.PGND$16 (PGND), SPM1-12V-5V.PGND$17 (PGND), SPM1-12V-5V.PGND$18 (PGND), SPM1-12V-5V.PGND$19 (PGND), SPM1-12V-5V.PGND$20 (PGND), SPM1-12V-5V.PGND$21 (PGND), SPM1-12V-5V.PGND$22 (PGND), SPM1-12V-5V.PGND$23 (PGND), SPM1-12V-5V.PGND$24 (PGND), SPM1-12V-5V.PGND$25 (PGND), SPM1-12V-5V.PGND$26 (PGND), SPM1-12V-5V.PGND$27 (PGND), SPM1-12V-5V.PGND$28 (PGND), SPM1-12V-5V.PGND$29 (PGND), SPM1-12V-5V.PGND$30 (PGND), SPM1-12V-5V.PGND$31 (PGND), SPM1-12V-5V.PGND$32 (PGND), SPM1-12V-5V.PGND$33 (PGND), SPM1-12V-5V.PGND$34 (PGND), ZE.1 (ANODE); also elsewhere on the board
M_MISO: M2515.17 (SO); also elsewhere on the board
M_MOSI: M2515.16 (SI); also elsewhere on the board
M_RST: M2515.19 (RESET/); also elsewhere on the board
M_SCK: M2515.14 (SCK); also elsewhere on the board
unnamed: CC2.P$2, CC4.P$1
unnamed: CC1.P$2, CC3.P$1
unnamed: M2551.8 (RS), R7.P$1
unnamed: 16MHZCAN.1, M2515.8 (OSC2)
unnamed: 16MHZCAN.3, M2515.9 (OSC1)
unnamed: RCAN1.P$2, RCAN2.P$1
unnamed: CC1.P$1, RCAN3.P$2
unnamed: CC2.P$1, RCAN4.P$2
unnamed: RCAN2.P$2, TERMINATE.2
PHASE_DND: SPM1-12V-5V.PHASE$1 (PHASE), SPM1-12V-5V.PHASE$2 (PHASE), SPM1-12V-5V.PHASE$3 (PHASE)
PWRGD: SPM1-12V-5V.PWRGD; also elsewhere on the board

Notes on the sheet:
CANBUS (C)
12V->5V (E)
5V->3.3V
CAN/POWER
OVP/PTC FUSES
TPSMA6L15A
ZEN164V130A24LS
*These are expensive, low supply, and only used to avoid unacceptably tall electrolytics. Alternatives would be preferred in production.
*The module is not "automotive grade": it was chosen for its size and switching nature, but it likely requires the extra protection I've added. It's also got 30W of capacity and costs $10, so it's fairly overkill (plus, the PPTC to the right limits it to ~15).
*Too much? Too little? "Just need" something else? No idea, feedback is welcome.
*I've had to rework these resonators twice. If more space was available, I'd move to proper, larger crystals.

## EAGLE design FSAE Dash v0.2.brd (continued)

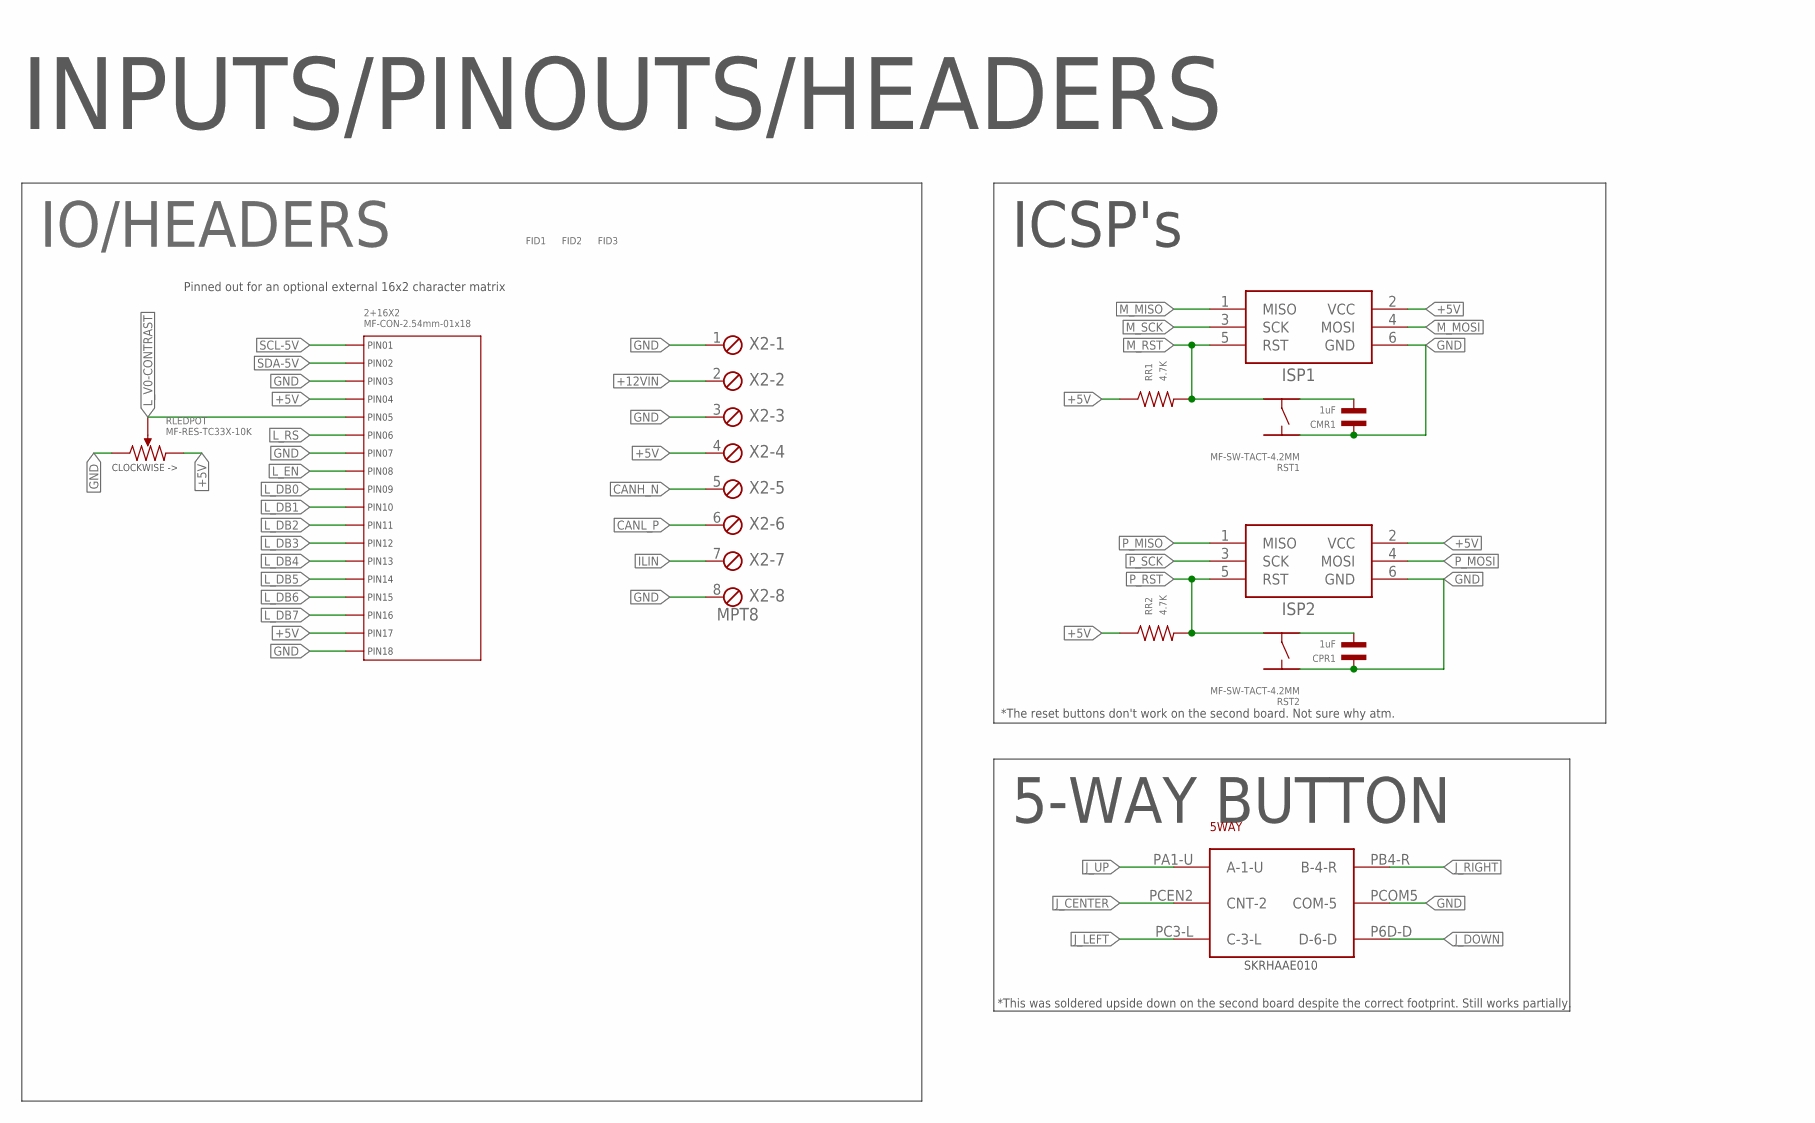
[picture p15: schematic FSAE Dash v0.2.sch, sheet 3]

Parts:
2+16X2: MF-CON-2.54mm-01x18; PTH_2.54MM_01X18
5WAY: SKRHAAE010; ALPS-SKRHAAE010
CMR1: 1uF; C0402
CPR1: 1uF; C0402
FID1, FID2, FID3: FIDUCIAL_100MIL
ISP1, ISP2: AVRISP-6; AVRISP
RLEDPOT: MF-RES-TC33X-10K; TC33
RR1, RR2: 4.7K; R0603
RST1, RST2: MF-SW-TACT-4.2MM; TACT4.2MM
X2: MPT8; 8POL254

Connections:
+5V: 2+16X2.P$4 (PIN4), 2+16X2.P$17 (PIN17), ISP1.2 (VCC), ISP2.2 (VCC), RLEDPOT.P$3, RR1.P$1, RR2.P$1, X2.4; also elsewhere on the board
+12VIN: X2.2; also elsewhere on the board
CANH_N: X2.5; also elsewhere on the board
CANL_P: X2.6; also elsewhere on the board
GND: 2+16X2.P$3 (PIN3), 2+16X2.P$7 (PIN7), 2+16X2.P$18 (PIN18), 5WAY.PCOM5 (COM-5), CMR1.P$1, CPR1.P$1, ISP1.6 (GND), ISP2.6 (GND), RLEDPOT.P$1, RST1.P$1, RST2.P$1, X2.1, X2.3, X2.8; also elsewhere on the board
ILIN: X2.7; also elsewhere on the board
J_CENTER: 5WAY.PCEN2 (CNT-2); also elsewhere on the board
J_DOWN: 5WAY.P6D-D (D-6-D); also elsewhere on the board
J_LEFT: 5WAY.PC3-L (C-3-L); also elsewhere on the board
J_RIGHT: 5WAY.PB4-R (B-4-R); also elsewhere on the board
J_UP: 5WAY.PA1-U (A-1-U); also elsewhere on the board
L_DB0: 2+16X2.P$9 (PIN9); also elsewhere on the board
L_DB1: 2+16X2.P$10 (PIN10); also elsewhere on the board
L_DB2: 2+16X2.P$11 (PIN11); also elsewhere on the board
L_DB3: 2+16X2.P$12 (PIN12); also elsewhere on the board
L_DB4: 2+16X2.P$13 (PIN13); also elsewhere on the board
L_DB5: 2+16X2.P$14 (PIN14); also elsewhere on the board
L_DB6: 2+16X2.P$15 (PIN15); also elsewhere on the board
L_DB7: 2+16X2.P$16 (PIN16); also elsewhere on the board
L_EN: 2+16X2.P$8 (PIN8); also elsewhere on the board
L_RS: 2+16X2.P$6 (PIN6); also elsewhere on the board
L_V0-CONTRAST: 2+16X2.P$5 (PIN5), RLEDPOT.P$2
M_MISO: ISP1.1 (MISO); also elsewhere on the board
M_MOSI: ISP1.4 (MOSI); also elsewhere on the board
M_RST: ISP1.5 (RST), RR1.P$2, RST1.P$4; also elsewhere on the board
M_SCK: ISP1.3 (SCK); also elsewhere on the board
unnamed: CPR1.P$2, RST2.P$3
unnamed: CMR1.P$2, RST1.P$3
P_MISO: ISP2.1 (MISO); also elsewhere on the board
P_MOSI: ISP2.4 (MOSI); also elsewhere on the board
P_RST: ISP2.5 (RST), RR2.P$2, RST2.P$4; also elsewhere on the board
P_SCK: ISP2.3 (SCK); also elsewhere on the board
SCL-5V: 2+16X2.P$1 (PIN1); also elsewhere on the board
SDA-5V: 2+16X2.P$2 (PIN2); also elsewhere on the board

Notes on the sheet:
IO/HEADERS
ICSP's
INPUTS/PINOUTS/HEADERS
5-WAY BUTTON
Pinned out for an optional external 16x2 character matrix
SKRHAAE010
*The reset buttons don't work on the second board. Not sure why atm.
*This was soldered upside down on the second board despite the correct footprint. Still works partially.

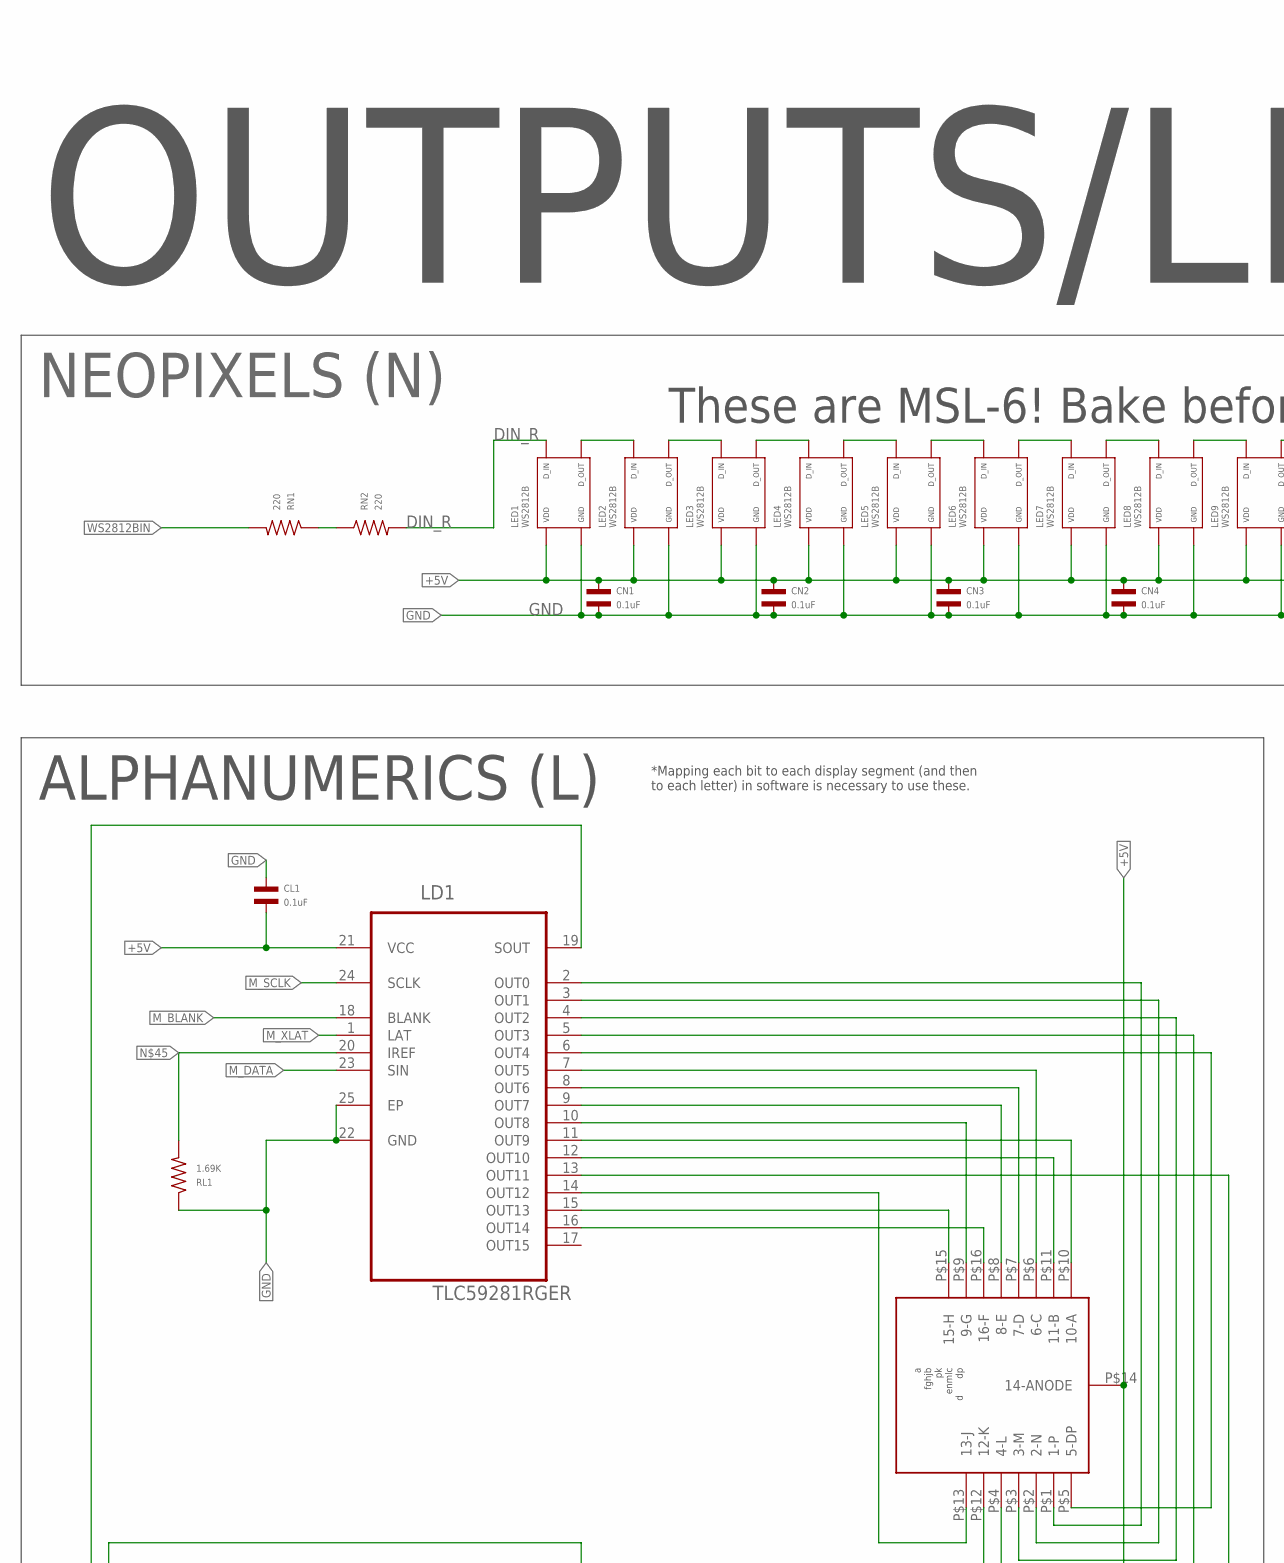
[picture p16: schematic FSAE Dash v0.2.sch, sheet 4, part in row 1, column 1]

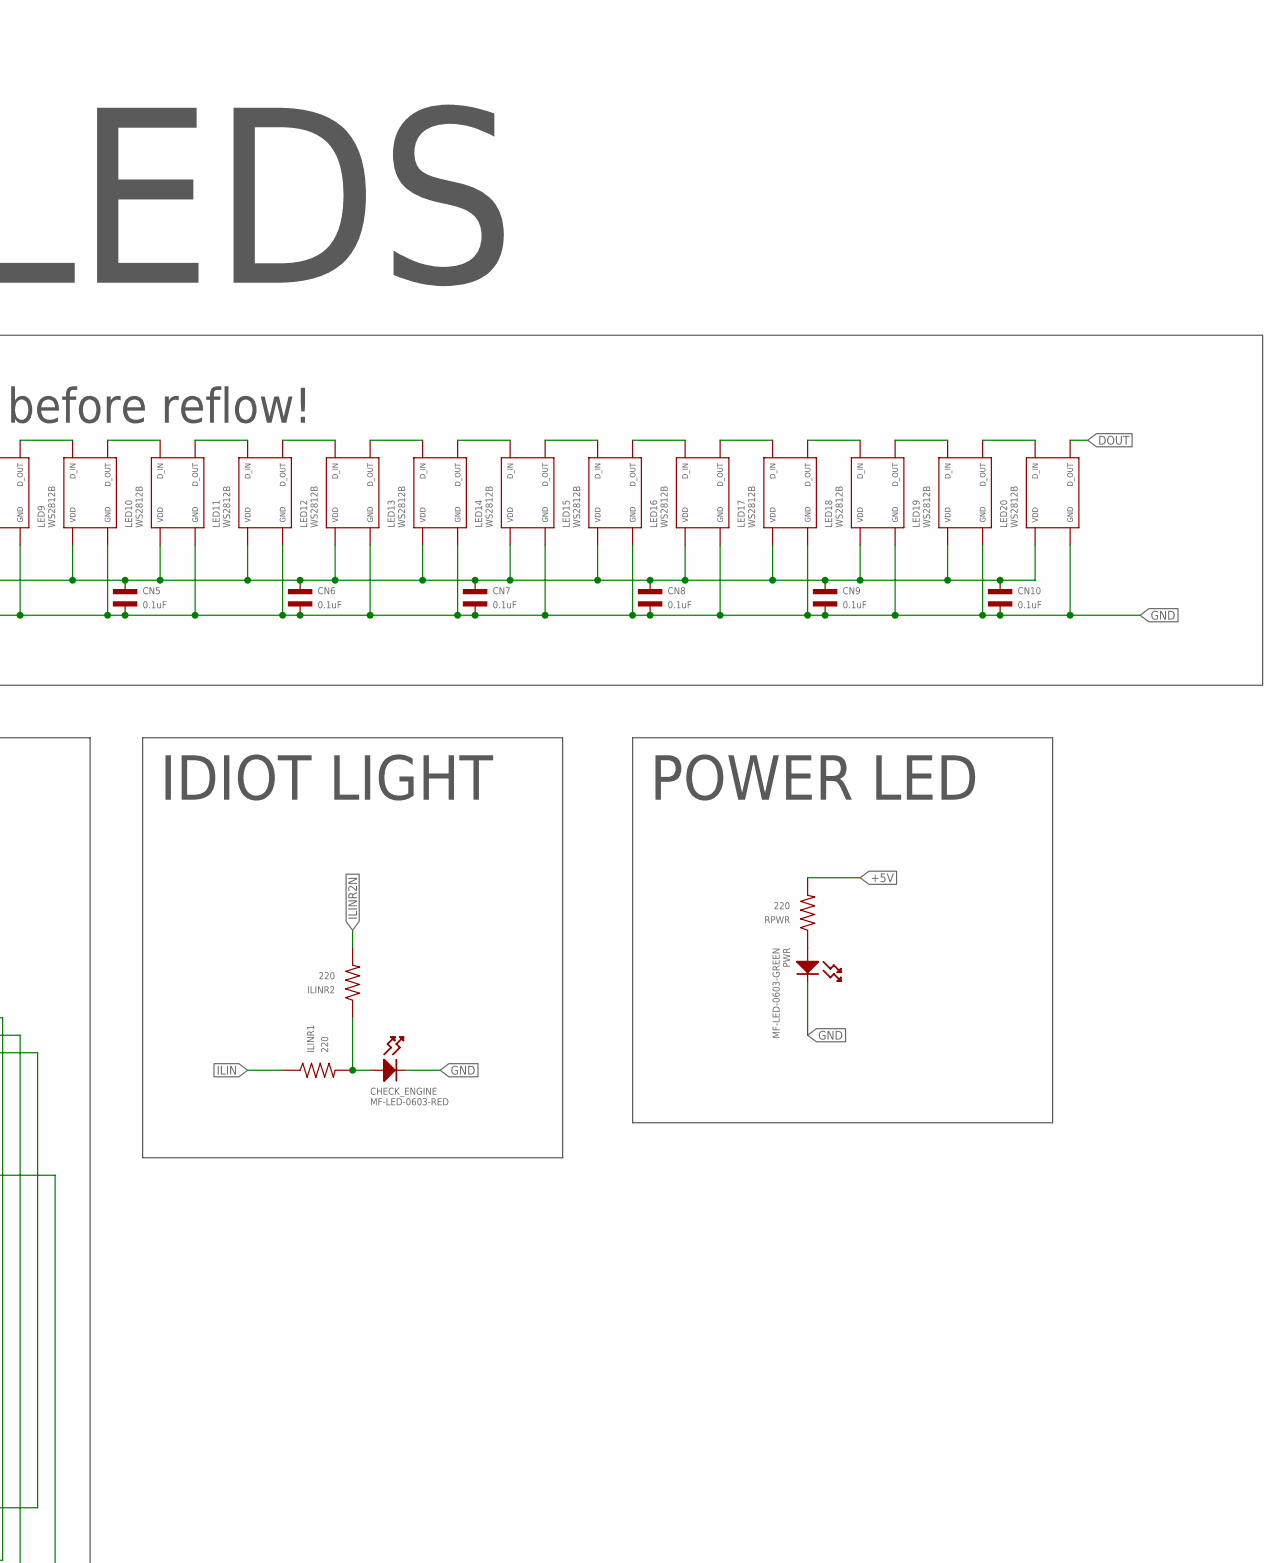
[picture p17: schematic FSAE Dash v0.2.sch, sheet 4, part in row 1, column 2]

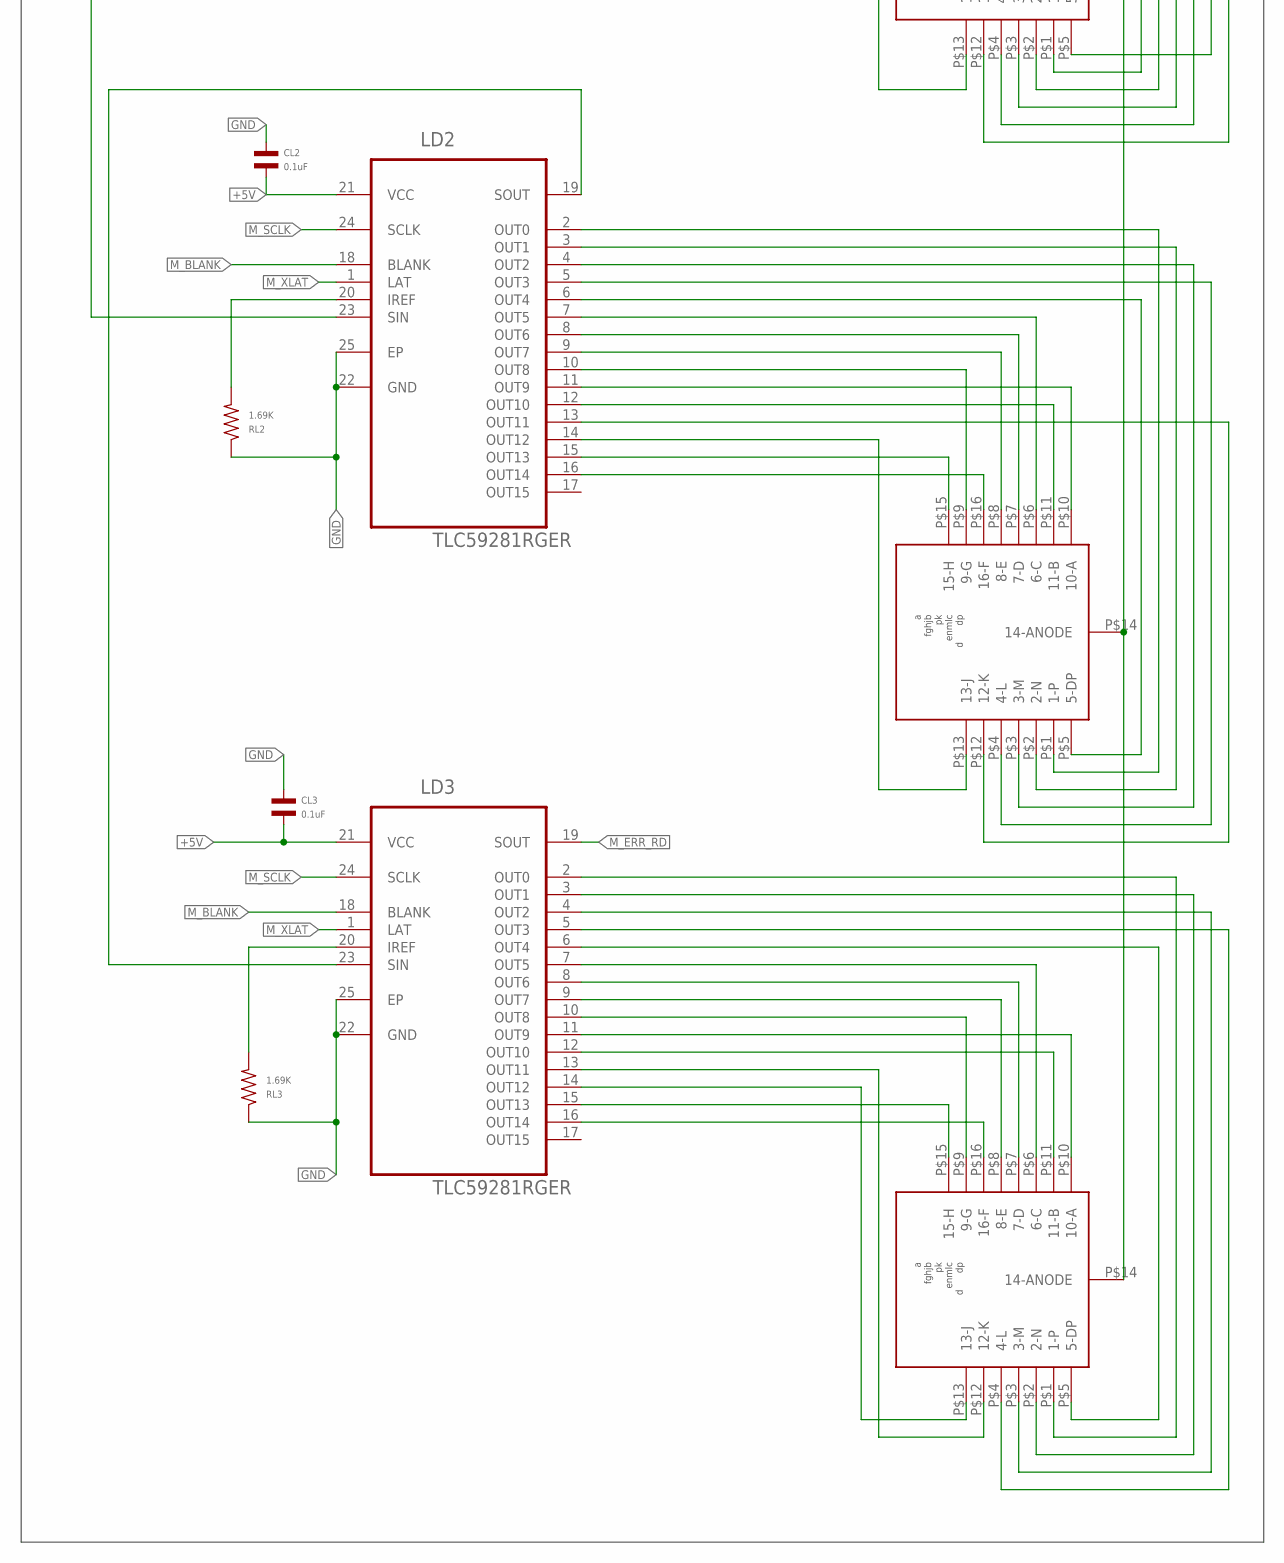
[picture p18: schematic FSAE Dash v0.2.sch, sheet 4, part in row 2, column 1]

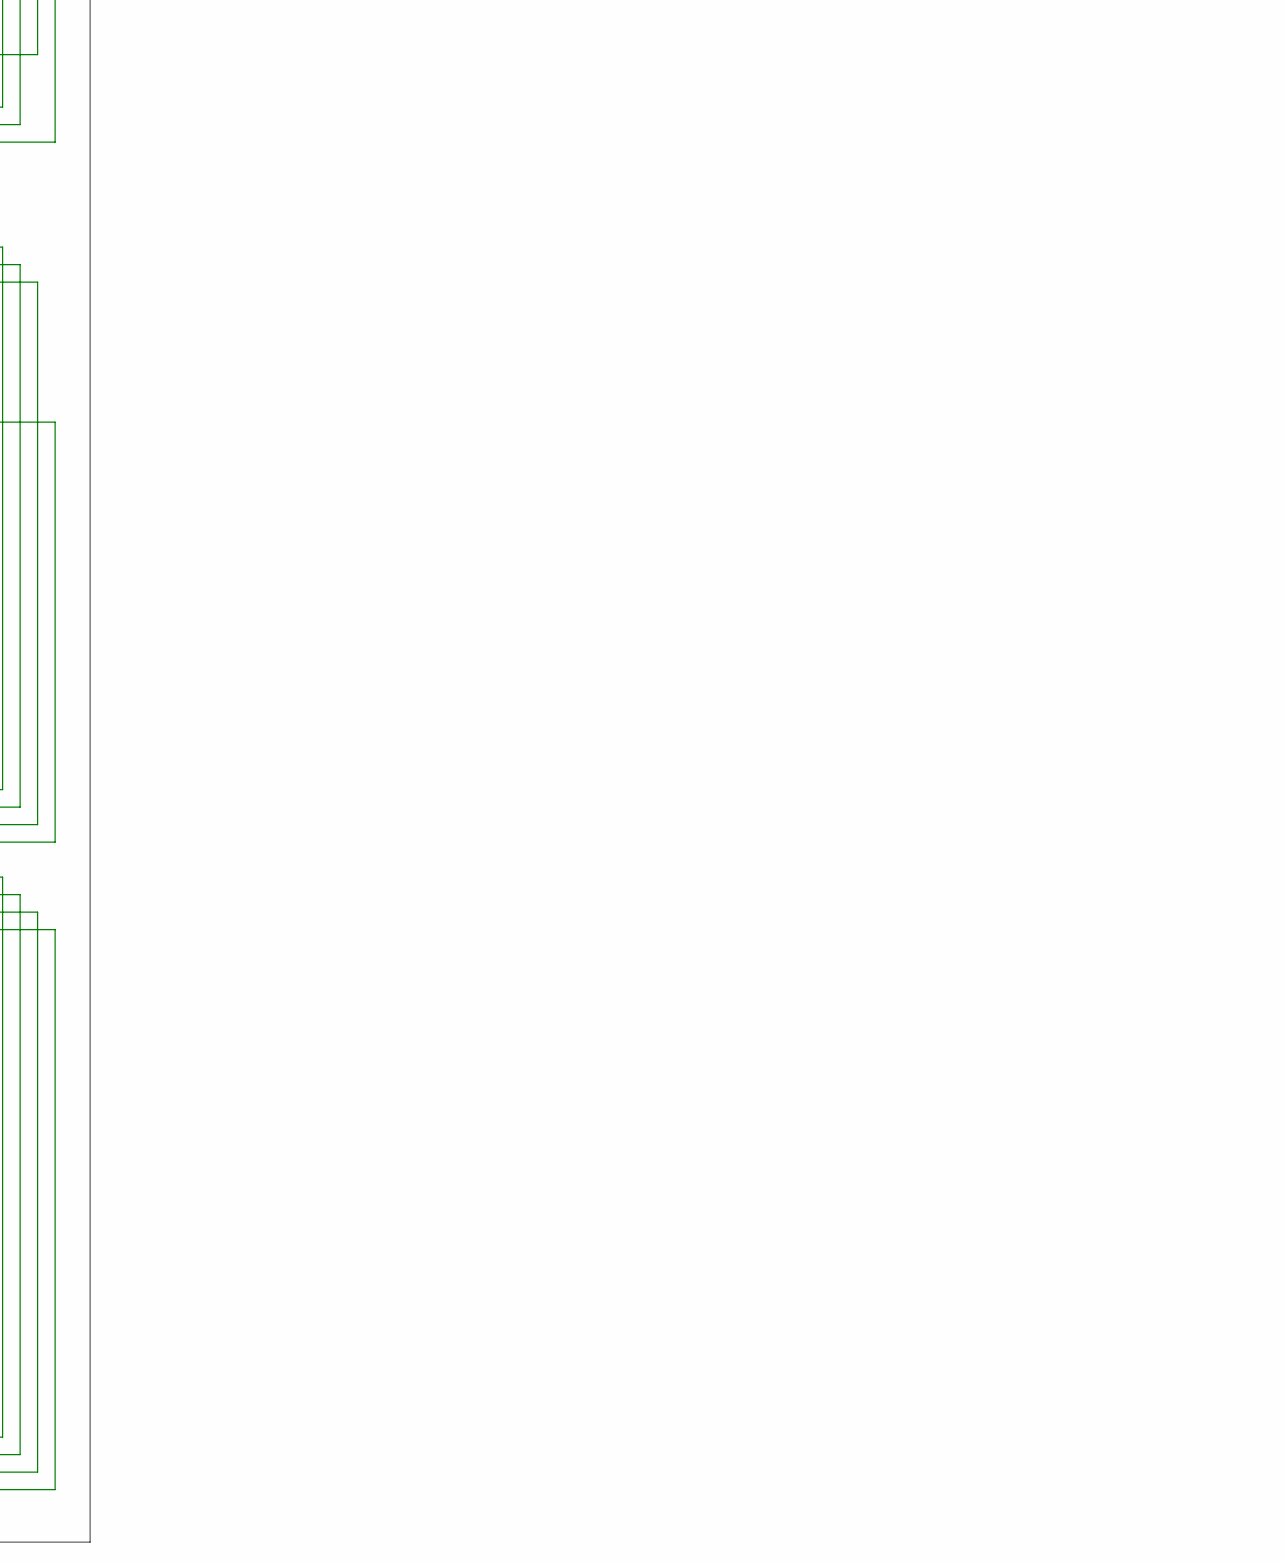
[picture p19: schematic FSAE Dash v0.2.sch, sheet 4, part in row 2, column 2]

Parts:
CHECK_ENGINE: MF-LED-0603-RED; LED0603
CL1, CL2, CL3: 0.1uF; C0402
CN1, CN2, CN3, CN4, CN5, CN6, CN7, CN8, CN9, CN10: 0.1uF; C0402
ILINR1, ILINR2: 220; R0402
L1, L2, L3: ACPSA04-41SYKWA
LD1, LD2, LD3: TLC59281RGER; QFN50P400X400X100-25N
LED1, LED2, LED3, LED4, LED5, LED6, LED7, LED8, LED9, LED10, LED11, LED12, LED13, LED14, LED15, LED16, LED17, LED18, LED19, LED20: WS2812B
PWR: MF-LED-0603-GREEN; LED0603
RL1, RL2, RL3: 1.69K; R0603
RN1, RN2: 220; R0402
RPWR: 220; R0402

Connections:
+5V: CL1.P$2, CL2.P$2, CL3.P$2, CN1.P$1, CN2.P$1, CN3.P$1, CN4.P$1, CN5.P$1, CN6.P$1, CN7.P$1, CN8.P$1, CN9.P$1, CN10.P$1, L1.P$14 (14-ANODE), L2.P$14 (14-ANODE), L3.P$14 (14-ANODE), LD1.21 (VCC), LD2.21 (VCC), LD3.21 (VCC), LED1.P$1 (VDD), LED2.P$1 (VDD), LED3.P$1 (VDD), LED4.P$1 (VDD), LED5.P$1 (VDD), LED6.P$1 (VDD), LED7.P$1 (VDD), LED8.P$1 (VDD), LED9.P$1 (VDD), LED10.P$1 (VDD), LED11.P$1 (VDD), LED12.P$1 (VDD), LED13.P$1 (VDD), LED14.P$1 (VDD), LED15.P$1 (VDD), LED16.P$1 (VDD), LED17.P$1 (VDD), LED18.P$1 (VDD), LED19.P$1 (VDD), LED20.P$1 (VDD), RPWR.P$2; also elsewhere on the board
DIN_R: LED1.P$4 (DIN), RN2.P$2
DOUT: LED20.P$2 (DOUT)
GND: CHECK_ENGINE.CATHODE, CL1.P$1, CL2.P$1, CL3.P$1, CN1.P$2, CN2.P$2, CN3.P$2, CN4.P$2, CN5.P$2, CN6.P$2, CN7.P$2, CN8.P$2, CN9.P$2, CN10.P$2, LD1.22 (GND), LD1.25 (EP), LD2.22 (GND), LD2.25 (EP), LD3.22 (GND), LD3.25 (EP), LED1.P$3 (VSS), LED2.P$3 (VSS), LED3.P$3 (VSS), LED4.P$3 (VSS), LED5.P$3 (VSS), LED6.P$3 (VSS), LED7.P$3 (VSS), LED8.P$3 (VSS), LED9.P$3 (VSS), LED10.P$3 (VSS), LED11.P$3 (VSS), LED12.P$3 (VSS), LED13.P$3 (VSS), LED14.P$3 (VSS), LED15.P$3 (VSS), LED16.P$3 (VSS), LED17.P$3 (VSS), LED18.P$3 (VSS), LED19.P$3 (VSS), LED20.P$3 (VSS), PWR.CATHODE, RL1.P$1, RL2.P$1, RL3.P$1; also elsewhere on the board
ILIN: ILINR1.P$1; also elsewhere on the board
ILINR2N: ILINR2.P$2; also elsewhere on the board
M_BLANK: LD1.18 (BLANK), LD2.18 (BLANK), LD3.18 (BLANK); also elsewhere on the board
M_DATA: LD1.23 (SIN); also elsewhere on the board
M_ERR_RD: LD3.19 (SOUT); also elsewhere on the board
M_SCLK: LD1.24 (SCLK), LD2.24 (SCLK), LD3.24 (SCLK); also elsewhere on the board
M_XLAT: LD1.1 (LAT), LD2.1 (LAT), LD3.1 (LAT); also elsewhere on the board
unnamed: LED1.P$2 (DOUT), LED2.P$4 (DIN)
unnamed: LED2.P$2 (DOUT), LED3.P$4 (DIN)
unnamed: LED3.P$2 (DOUT), LED4.P$4 (DIN)
unnamed: LED4.P$2 (DOUT), LED5.P$4 (DIN)
unnamed: LED5.P$2 (DOUT), LED6.P$4 (DIN)
unnamed: LED6.P$2 (DOUT), LED7.P$4 (DIN)
unnamed: LED7.P$2 (DOUT), LED8.P$4 (DIN)
unnamed: PWR.ANODE, RPWR.P$1
unnamed: LED8.P$2 (DOUT), LED9.P$4 (DIN)
unnamed: LED9.P$2 (DOUT), LED10.P$4 (DIN)
unnamed: LED10.P$2 (DOUT), LED11.P$4 (DIN)
unnamed: LED11.P$2 (DOUT), LED12.P$4 (DIN)
unnamed: LED12.P$2 (DOUT), LED13.P$4 (DIN)
unnamed: LED13.P$2 (DOUT), LED14.P$4 (DIN)
unnamed: LED14.P$2 (DOUT), LED15.P$4 (DIN)
unnamed: LED15.P$2 (DOUT), LED16.P$4 (DIN)
unnamed: LED16.P$2 (DOUT), LED17.P$4 (DIN)
unnamed: LED17.P$2 (DOUT), LED18.P$4 (DIN)
unnamed: LED18.P$2 (DOUT), LED19.P$4 (DIN)
unnamed: LED19.P$2 (DOUT), LED20.P$4 (DIN)
unnamed: CHECK_ENGINE.ANODE, ILINR1.P$2, ILINR2.P$1
unnamed: RN1.P$1, RN2.P$1
unnamed: LD1.20 (IREF), RL1.P$2
unnamed: LD1.19 (SOUT), LD2.23 (SIN)
unnamed: L3.P$1 (1-P), LD3.2 (OUT0)
unnamed: LD2.20 (IREF), RL2.P$2
unnamed: LD2.19 (SOUT), LD3.23 (SIN)
unnamed: LD3.20 (IREF), RL3.P$2
unnamed: L3.P$2 (2-N), LD3.3 (OUT1)
unnamed: L3.P$3 (3-M), LD3.4 (OUT2)
unnamed: L3.P$4 (4-L), LD3.5 (OUT3)
unnamed: L3.P$5 (5-DP), LD3.6 (OUT4)
unnamed: L3.P$6 (6-C), LD3.7 (OUT5)
unnamed: L3.P$7 (7-D), LD3.8 (OUT6)
unnamed: L3.P$8 (8-E), LD3.9 (OUT7)
unnamed: L3.P$9 (9-G), LD3.10 (OUT8)
unnamed: L3.P$10 (10-A), LD3.11 (OUT9)
unnamed: L3.P$11 (11-B), LD3.12 (OUT10)
unnamed: L3.P$12 (12-K), LD3.13 (OUT11)
unnamed: L3.P$13 (13-J), LD3.14 (OUT12)
unnamed: L3.P$15 (15-H), LD3.15 (OUT13)
unnamed: L3.P$16 (16-F), LD3.16 (OUT14)
unnamed: L2.P$1 (1-P), LD2.2 (OUT0)
unnamed: L2.P$2 (2-N), LD2.3 (OUT1)
unnamed: L2.P$3 (3-M), LD2.4 (OUT2)
unnamed: L2.P$4 (4-L), LD2.5 (OUT3)
unnamed: L2.P$5 (5-DP), LD2.6 (OUT4)
unnamed: L2.P$6 (6-C), LD2.7 (OUT5)
unnamed: L2.P$7 (7-D), LD2.8 (OUT6)
unnamed: L2.P$8 (8-E), LD2.9 (OUT7)
unnamed: L2.P$9 (9-G), LD2.10 (OUT8)
unnamed: L2.P$10 (10-A), LD2.11 (OUT9)
unnamed: L2.P$11 (11-B), LD2.12 (OUT10)
unnamed: L2.P$12 (12-K), LD2.13 (OUT11)
unnamed: L2.P$13 (13-J), LD2.14 (OUT12)
unnamed: L2.P$15 (15-H), LD2.15 (OUT13)
unnamed: L2.P$16 (16-F), LD2.16 (OUT14)
unnamed: L1.P$1 (1-P), LD1.2 (OUT0)
unnamed: L1.P$2 (2-N), LD1.3 (OUT1)
unnamed: L1.P$3 (3-M), LD1.4 (OUT2)
unnamed: L1.P$4 (4-L), LD1.5 (OUT3)
unnamed: L1.P$5 (5-DP), LD1.6 (OUT4)
unnamed: L1.P$6 (6-C), LD1.7 (OUT5)
unnamed: L1.P$7 (7-D), LD1.8 (OUT6)
unnamed: L1.P$8 (8-E), LD1.9 (OUT7)
unnamed: L1.P$9 (9-G), LD1.10 (OUT8)
unnamed: L1.P$10 (10-A), LD1.11 (OUT9)
unnamed: L1.P$11 (11-B), LD1.12 (OUT10)
unnamed: L1.P$12 (12-K), LD1.13 (OUT11)
unnamed: L1.P$13 (13-J), LD1.14 (OUT12)
unnamed: L1.P$15 (15-H), LD1.15 (OUT13)
unnamed: L1.P$16 (16-F), LD1.16 (OUT14)
WS2812BIN: RN1.P$2; also elsewhere on the board

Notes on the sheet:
ALPHANUMERICS (L)
IDIOT LIGHT
POWER LED
NEOPIXELS (N)
OUTPUTS/LEDS
These are MSL-6! Bake before reflow!
*Mapping each bit to each display segment (and then to each letter) in software is necessary to use these.

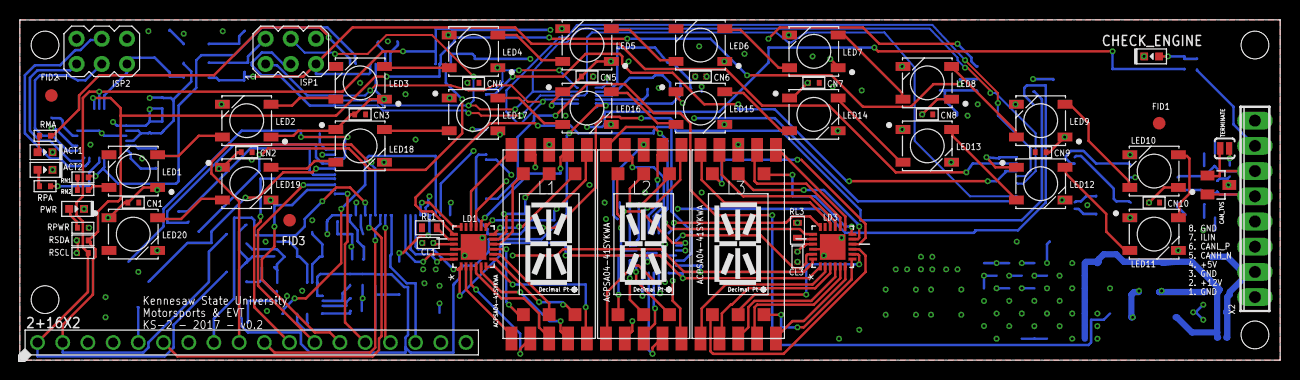
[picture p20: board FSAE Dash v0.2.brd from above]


Board: 4 copper layers, 127.0 x 34.3 mm, 143 parts (84 on the bottom side), 161 nets.

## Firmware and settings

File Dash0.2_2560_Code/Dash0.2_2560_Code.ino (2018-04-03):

//----------------------- MEGA/2560

/*
  KSU Motorsports/FSAE KS-2 Dashboard ATmega2560 Firmware
  Clinton Flowers, 2017
  For programming via ISP, see https://learn.sparkfun.com/tutorials/installing-an-arduino-bootloader/connecting-the-programmer
  Don't forget the capacitor on the reset pin of the programmer Arduino, and don't forget to use "Upload using Programmer"
  
  If you're using this for a student project (e.g., a Formula SAE car) and need help with it feel free to contact me @ clintonflowers222@gmail.com
  
  Remember, a design goal of this dash was to display only critical information the driver needs to know; K.I.S.S. applies. If this changes, consider Waveshare panels.
  
  MSCan_Sniffer was used and is Copyright (c) 2013 David Will - davidwill@gmail.com The MIT License (MIT)
 */

// Note - CAN data is transmitted in the blind.
// Communications with Megasquirt can only be verified by *RECEIVED* data.
#define MS_REQUEST

#include <SPI.h>
#include <Wire.h>
#include "RTClib.h" // Adafruit RTCLib Library, from Library Manager
#include <SD.h>
// IMU Includes
#include <Adafruit_Sensor.h> // Adafruit Unified Sensor library, from Library Manager
#include <Adafruit_BNO055.h> // Adafruit BNO055 library, from Library Manager
#include <utility/imumaths.h>
//#define BNO055_SAMPLERATE_DELAY_MS (10) // 1s / 10ms = 100Hz

#define WATCHDOG
#ifdef WATCHDOG
#include <avr/wdt.h> // Watchdog timer for possible lock-ups
#endif

#define DEBUG
#ifdef DEBUG
#define debugShow(x) show(x)
#else
#define debugShow(x)
#endif

// Pin definitions specific to how the MCP2515 is wired up.
// If this code is being breadboarded off of the actual PCB: Pin 10 for SparkFun canbus shield
#define CS_PIN    36
#define CAN_INT_PIN   18 // INTERRUPT != PIN. 
/* 
 Board  int.0 int.1 int.2 int.3 int.4 int.5
 Uno, Ethernet  2 3        
 Mega2560 2 3 21  20  19  18
 Leonardo 3 2 0 1 7  
*/

// These arrays are used to map the alphanumeric LED's to the associated code character. 
// Each bit position corresponds to a segment of the LED; adding the correct bits together and then shifting that byte into the driver will light up the segments for that character
// Since there are 15 positions per digit, we use 2 8-bit bytes, so a Top and a Bottom
const char characterList[] =    {' ',  '$',  '0',  '1',  '2',  '3',  '4',  '5',  '6',  '7',  '8',  '9',  'A',  'B',  'C',  'D',  'E',  'F',  'G',  'H',  'I',  'J',  'K',  'L',  'M',  'N',  'O',  'P',  'Q',  'R',  'S',  'T',  'U',  'V',  'W',  'X',  'Y',  'Z'};
const byte characterBottoms[] = {0x00, 0x65, 0xe2, 0x20, 0xc1, 0x61, 0x21, 0x61, 0xe1, 0x20, 0xe1, 0x21, 0xa1, 0x65, 0xc0, 0x64, 0xc1, 0x81, 0xe0, 0xa1, 0x44, 0xe0, 0x89, 0xc0, 0xa0, 0xa8, 0xe0, 0x81, 0xe8, 0x89, 0x60, 0x04, 0xe0, 0x82, 0xaa, 0x0a, 0x05, 0x42};
const byte characterTops[] =    {0x00, 0x6a, 0x56, 0x14, 0x0e, 0x0e, 0x4c, 0x4a, 0x4a, 0x06, 0x4e, 0x4e, 0x4e, 0x2e, 0x42, 0x26, 0x42, 0x42, 0x4a, 0x4c, 0x22, 0x04, 0x50, 0x40, 0x55, 0x45, 0x46, 0x4e, 0x46, 0x4e, 0x0b, 0x22, 0x44, 0x50, 0x44, 0x11, 0x4c, 0x12};
// Various control variables for the TLC59281RGER Constant Current LED Driver
const int blankPin = 65;
const int latchPin = 64;
const int clockPin = 63;
const int dataPin = 62;
// Pins for the joystick on the rear of the device, accounting for improper hardware placement. Unused in current code.
const int centerPin = PE6;  // Center in schematic, J_Common as installed. 
const int rightPin = 19;    // J_Left in schematic
const int leftPin = PE7;    // J_Right in schematic
const int downPin = 2;      // J_Up in schematic
const int upPin = 3;        // J_Down in schematic
// How many (14-segment + dp) alphanumeric displays are connected
const int numberOfAlphanumerics = 3;
// Vars for data passed to shifting function
byte dataOne, dataTwo, dataThree, dataFour, dataFive, dataSix;

//MCP2515 definitions, from the MSCAN_Sniffer Code
// May be improved by throwing all of this into an external included file
#define CAN_READ        0x03
#define CAN_WRITE       0x02
#define CANINTE         0x2B
#define CANINTF         0x2C
#define BFPCTRL         0x0C
#define CANCTRL         0x0F
#define CANSTAT         0x0E

#define CNF1            0x2A
#define CNF2            0x29
#define CNF3            0x28
#define RXB0CTRL        0x60
#define RXB1CTRL        0x70

// TX Buffer 0
#define TXB0CTRL        0x30
#define TXB0SIDH        0x31
#define TXB0SIDL        0x32
#define TXB0EID8        0x33
#define TXB0EID0        0x34
#define TXB0DLC         0x35
#define TXB0D0          0x36
#define TXB0D1          0x37
#define TXB0D2          0x38
#define TXB0D3          0x39
#define TXB0D4          0x3A
#define TXB0D5          0x3B
#define TXB0D6          0x3C
#define TXB0D7          0x3D
// RX Buffer 0
#define RXB0CTRL        0x60
#define RXB0SIDH        0x61
#define RXB0SIDL        0x62
#define RXB0EID8        0x63
#define RXB0EID0        0x64
#define RXB0DLC         0x65
#define RXB0D0          0x66
#define RXB0D1          0x67
#define RXB0D2          0x68
#define RXB0D3          0x69
#define RXB0D4          0x6A
#define RXB0D5          0x6B
#define RXB0D6          0x6C
#define RXB0D7          0x6D
// RX Buffer 1
#define RXB1CTRL        0x70
#define RXB1SIDH        0x71
#define RXB1SIDL        0x72
#define RXB1EID8        0x73
#define RXB1EID0        0x74
#define RXB1DLC         0x75
#define RXB1D0          0x76
#define RXB1D1          0x77
#define RXB1D2          0x78
#define RXB1D3          0x79
#define RXB1D4          0x7A
#define RXB1D5          0x7B
#define RXB1D6          0x7C
#define RXB1D7          0x7D

// Global vars aren't ideal but they simplify the coding process, especially with a substandard IDE or on a microcontroller.
byte SIDH, SIDL, EID8, EID0, DLC;
byte databuffer[7];
unsigned int data; 
byte block, canintf;
unsigned int offset;
byte dataready = 0;
long lastISR = 0;
long lastParse = 0;
volatile long lastMillisInt = 5000; // don't PWM the screen before this many ms
volatile bool lastMillisIntState = LOW;
volatile bool displayingText = true;
long lastShow = 0;

// Fields stored as received over CAN bus. Append new variables of interest here.
// After declaring the variable storage here, add code to request the associated address in the loop, and handle it in the ISR
// One better way to do this would be object-oriented, where the CAN fields are instantiated with name, address, etc, and add themselves to an array of CAN field objects
unsigned int canRPM = 0;
unsigned const int shiftRPM = 12000;
String canVoltage = "0";
int canTPS = 0;
int canGear = 10; // Zeroeth gear = maybe neutral
int canCELStatus = 0; // CANbus Check Engine Light status
int canTPSADC = 0;
int canCELErrorCode = 0;
int canCLT = 0;
int canOLP = -1; // Oil pressure

// Clock (DS3231), IMU (BNO055) Setup
RTC_DS3231 rtc;
Adafruit_BNO055 bno = Adafruit_BNO055();
imu::Vector<3> accel;
int latAccel = 0;
// I2C Addresses
const int unoAddress = 5;
const int megaAddress = 6;

void setup() {
  // Enable Watchdog Timer
  wdt_enable(WDTO_8S); // 8 seconds to allow for programming on ...most... bootloaders. :contingency:
  // TODO: For when the dash reboots mid-race due to any reason, maybe make this ask the other MCU its millis() over I2C to see if it should say "hooty hoo" etc, or jump right into displaying RPM
  
  pinMode(CS_PIN, OUTPUT);
  SPI.setClockDivider(SPI_CLOCK_DIV2);
  SPI.setDataMode(SPI_MODE0);
  SPI.setBitOrder(MSBFIRST);
  SPI.begin();
  delay(1);
  // Check MCP2515 whitepaper for option definitions. These work for Megasquirt.
  CANWrite(CANCTRL, B10000111); // Set MCP2515 to config mode
  CANWrite(CNF1, 0x00); // CNF1 b00000000
  CANWrite(CNF2, 0xA4); // CNF2 b10100100
  CANWrite(CNF3, 0x84); // CNF3 b10000100
  CANWrite(CANCTRL, B00000111); // Set MCP2515 to normal mode
  delay(1);
  CANWrite(RXB0CTRL, B01101000); //RXB0CTRL clear receive buffers
  CANWrite(RXB1CTRL, B01101000); //RXB1CTRL clear receive buffers
  CANWrite(CANINTE, B00000011); // Enable interrupt on RXB0, RXB1
  CANWrite(BFPCTRL, B00001111); // setting interrupts 

  // Joystick interrupts. 
//  pinMode(centerPin, OUTPUT);
//  pinMode(upPin, INPUT_PULLUP);
//  pinMode(downPin, INPUT_PULLUP);
//  pinMode(leftPin, INPUT_PULLUP);
//  pinMode(rightPin, INPUT_PULLUP);
//  digitalWrite(centerPin, LOW);  // Ground the "common" pin (as installed)
//  attachInterrupt(digitalPinToInterrupt(downPin), resetFunction, FALLING);
//  attachInterrupt(digitalPinToInterrupt(upPin), upFunc, FALLING);
//  attachInterrupt(digitalPinToInterrupt(downPin), downFunc, FALLING);
//  attachInterrupt(digitalPinToInterrupt(leftPin), leftFunc, FALLING);
//  attachInterrupt(digitalPinToInterrupt(rightPin), rightFunc, FALLING);

  delay(1);
  Wire.begin(megaAddress);                // Join I2C bus with the address. See 328p code to guarantee its address if uncertain. 
  Wire.setClock(400000L);

  // Config for shiftOut, used for LED drivers
  pinMode(clockPin, OUTPUT);
  pinMode(dataPin, OUTPUT);
  pinMode(latchPin, OUTPUT);
  pinMode(blankPin, OUTPUT);

  // Timer interrupt on millis. IIRC this is used for TIMER0_COMPA_vect, to dim the alphanumerics by putting them on a ~50% duty cycle.
  OCR0A = 0xAF;
  TIMSK0 |= _BV(OCIE0A);

  // IMU Stuff
  if(!bno.begin()){
    showText("NIM"); // No BNO/IMU Detected. Hardware problem!
    delay(200);
  }
  delay(2);
  bno.setExtCrystalUse(true);
  delay(2);
  
  // DS3231 Clock Stuff
  if (! rtc.begin()) {
    showText("NCK"); // The Clock doesn't work. Hardware problem!
    delay(200);
  }
  
  if (rtc.lostPower()) {
    //rtc.adjust(DateTime(F(__DATE__), F(__TIME__)));
    // TODO: Make a clock synchronization procedure 
  }
  delay(1);
  DateTime now = rtc.now();
  delay(1);
  //showText("T " + String(now.hour()) + "." + String(now.minute()) + "." + String(now.second())); // Display the time (uncomment when setting time)
  delay(1);

  // SD Card / Datalogging Stuff
  // See the IR Tire Temp Sensor code on how to create files and handle appending/creating CSVs. Ensure the clocks are synced (DS3231 drifts ~5 seconds/month)
//  if (!SD.begin(A8)) { // The SD card CS line is on pin PC0/Arduino 37/A8 on Dash v0.2
//    showText("NSD");  // No SD card. User or hardware problem.
//    delay(200);
//  }else{
//    showText("SD.");
//    delay(200);
//  }
 
  showText("Hooty Hoo 1.9"); // Firmware version number.
  delay(100);

  // CAN Interrupt setup and CAN stuff
  pinMode(CAN_INT_PIN, INPUT_PULLUP); // Maybe not necessary, but shouldn't hurt
  attachInterrupt(digitalPinToInterrupt(CAN_INT_PIN), ISR_can, FALLING);
  for(int i = 0; i < 3; i++){
    MS_Parse();
    delay(1);
  }
} // End setup()

void loop() {
  // Clear watchdog, delaying forced resets. Sometimes called "kicking" the watchdog
#ifdef WATCHDOG
  wdt_reset();
#endif
// Check engine light test code. This is commented out since I couldn't get the ECU to actually report check engine light status from its CAN address(es)... Maybe it's bugged?
//  if(canCELStatus > 0){ // If there's a CEL status other than 0, display that fact
//    showText("CHK.");
//    delay(100);
//    showText(String(canCELStatus));
//    delay(100);
//  } else if(canCELErrorCode > 0){ // Check for error codes from the other CAN address
//    showText("CEL");
//    delay(100);
//    showText(String(canCELErrorCode));
//    delay(100);
//  } else{
//  }
  sendRpm(); // Send RPM to the 328P via I2C
  delay(1);
  accel = bno.getVector(Adafruit_BNO055::VECTOR_ACCELEROMETER);
  delay(1); // Allow time for fetching data from the IMU
  latAccel = accel.y();
  if(latAccel > 5){ // Display lateral G's if turning hard enough (over 5 m/s^2)
    float latGs = accel.y() / 9.81;
    showText(String(latGs));
  }else if(millis() % 5000 < 2500){
    // If the modulo of the time the dash has been on is < 2.5s, show voltage, otherwise show coolant temp.
    // (That's the programming way of saying alternate showing Batt and CLT every 2.5s)
    showText(String(canVoltage));
  }else{
    showText(String(canCLT));   // Coolant Temp
    //showText(String(canOLP)); // Oil Pressure
  }
    
  
  if (dataready == 1) {
    //MS_Parse(); // Deal with data if it's arrived (shouldn't be necessary since ISR_CAN is working)
    //dataready = 0;
  }else{
    #ifdef MS_REQUEST
    // See http://www.msextra.com/doc/pdf/Megasquirt_CAN_Broadcast.pdf for addresses
    MSrequest(7, 24, 2); // MS3 1.3.2 Firmware TPS - block 7, offset 24, 2 byte request
    delay(1); // Don't request stuff over CAN before it can be transmitted, received, and processed. Usually happens way under 1 ms--see oscilloscope traces.
    MSrequest(7, 26, 2); // MS3 1.3.2 Firmware batt - block 7, offset 26, 2 byte request
    delay(1);
    MSrequest(7, 6, 2); // MS3 1.3.2 Firmware RPM - block 7, offset 6, 2 byte request
    delay(1);
    MSrequest(7, 22, 2); // MS3 1.3.2 Firmware CLT - block 7, offset 22, 2 byte request
    delay(1);
    //MSrequest(7, 106, 2); // MS3 1.3.2 Firmware Generic In (Oil Pressure!(?)) - block 7, offset 106, 2 byte request
    //delay(1);
    //MSrequest(7, 270, 1); // MS3 1.3.2 Firmware gear - block 7, offset 270, 1 byte request
    //delay(1); 
    //MSrequest(7, 434, 2); // MS3 1.3.2 Firmware CEL Status - block 7, offset 434, 2 byte request
    //delay(1);
    //MSrequest(7, 226, 2); // MS3 1.3.2 Firmware TPSADC - block 7, offset 226, 2 byte request
    //delay(1);
    //MSrequest(7, 415, 1); // MS3 1.3.2 Firmware CEL Error Code - block 7, offset 415, 1 byte request
    //delay(1);
    #endif
  }
} // End loop()

void resetFunction() { // Software reset - first, try the watchdog timer
  wdt_disable();
  wdt_enable(WDTO_15MS);
  delay(16000); // Try to suicide via watchdog
  while(1){};
} // End reset function

// For debugging/testing the joystick
void upFunc(){
  showText("U");
  delay(100);
}
void downFunc(){
  showText("D");
  delay(100);
}
void leftFunc(){
  showText("L");
  delay(100);
}
void rightFunc(){
  showText("R");
  delay(100);
}

// I2C RequestEvent - Any time the 328P (assumed) requests data from the 2560 over I2C, respond with data
// In the later versions, this is not used, since the 2560 sends the 328P the RPM on its own time. Could delete.
void requestEvent(){
  if(canRPM == 0){ // The RPM is reading zero. Display TPS!
    Wire.write(map(canTPS, 0, 1050, 0, 255));
  }else{
    // Return the RPM value
    Wire.write(map(canRPM, 0, shiftRPM, 0, 255));
  }
} // End requestEvent()

// I2C Send RPM - When called, transmits the current RPM to the I2C Slaved 328P
void sendRpm(){
  // ledArgs format: setPixelGroup(int beginPixels, int endPixels, int delayTime, int red, int green, int blue, int mode). See 328p code for most up-to-date format.
  int ledArgs[7] = {1, 1, 0, 0, 40, 10, 0};
  Wire.beginTransmission(unoAddress);
  if(canRPM == 0){ // The RPM is reading zero - The engine is ostensibly off. Display TPS or something!
    ledArgs[1] = map(canTPS, 0, 1050, 0, 10); // Display a TPS reading
    if(canTPS == 0){
      // The TPS and RPM are both exactly zero, so CAN probably isn't working or the ECU is off. 
      // Might as well display the lateral acceleration or something so we know the dash isn't broken when debugging on a bench.
      ledArgs[1] = abs(latAccel);
      if(latAccel > 8){
        showText("ACC"); // Accelerometer/Acceleration
        delay(200);
      }
    }
  }else{
    // Display the RPM value
    ledArgs[3] = 128;   // Red
    ledArgs[4] = 50;    // Green
    ledArgs[5] = 0;     // Blue
    ledArgs[1] = map(canRPM, 0, shiftRPM, 0, 10);
    if(canRPM > shiftRPM){ // We're over 'n'k RPM, display bright blue/green. Don't use bright red since that should only indicate errors.
      ledArgs[3] = 64;
      ledArgs[4] = 128;
      ledArgs[5] = 255;
    }else if(canRPM > (shiftRPM * 2)){
      resetFunction(); // Something's broke, or breaking
    }
  }
  // Send the LED values to the 328P for display
  for(int i = 0; i < 7; i++){
    Wire.write(ledArgs[i]);
  }
  Wire.endTransmission();
} // End sendRpm()


// Main CAN Requester Function, from David Will's MSCan library
void MSrequest(byte block, unsigned int offset, byte req_bytes) {
  /* Request data in Megasquirt format */
  byte SIDH, SIDL, EID8, EID0, DLC, D0, D1, D2;
  //
  SIDH = lowByte(offset  >> 3);
  // var_offset<2:0> SRR IDE msg_type <3:0>
  SIDL = (lowByte((offset << 5)) | B0001000); //set IDE bit
  //      MFFFFTTT msg_type, From, To
  EID8 = B10011000; //:7 msg_req, from id 3 (4:3)
  //      TBBBBBSS To, Block, Spare
  EID0 = ( ( block & B00001111) << 3); // last 4 bits, move them to 6:3
  EID0 = ((( block & B00010000) >> 2) | EID0); // bit 5 goes to :2
  //
  DLC = B00000011;
  D0=(block);
  D1=(offset >> 3);
  D2=(((offset & B00000111) << 5) | req_bytes); // shift offset
  // Disable interrupts to prevent locking up during SPI transfers
  noInterrupts();
  //  digitalWrite(CS_PIN,LOW);
  PORTC &= B11111101; // Set CS pin (port C1, pin 36) low, starting a write
  SPI.transfer(0x40); // Push bits starting at 0x31 (RXB0SIDH)
  SPI.transfer(SIDH); //0x31
  SPI.transfer(SIDL); //0x32
  SPI.transfer(EID8); //0x33
  SPI.transfer(EID0); //0x34
  SPI.transfer(DLC);  //0x35
  SPI.transfer(D0); // 0x36 TXB0D0 my_varblk
  SPI.transfer(D1); // 0x37 TXB0D1 my_offset
  SPI.transfer(D2); // 0x38 TXB0D2 - request 8 bytes(?) from MS3
  //  digitalWrite(CS_PIN,HIGH); // end write
  PORTC |= B00000010; // Set CS pin (port C1, pin 36) high, ending the write
  
  // RTS - Send this buffer down the wire
  //  digitalWrite(CS_PIN,LOW);
  PORTC &= B11111101; // Set CS pin (port C1, pin 36) low, starting a write
  SPI.transfer(B10000001);
  //  digitalWrite(CS_PIN,HIGH);
  PORTC |= B00000010; // Set CS pin (port C1, pin 36) high, ending the write
  interrupts(); // *Don't* move this below CANWrite. Though maybe remove the redundant CANWrite.
  CANWrite(CANINTF,0x00); // Reenabling interrupts above this makes it freeze occasionally, 
                          // but enabling them afterwards below slows loops down a lot
} // End MSrequest()


// CAN Interrupt Service Routine Handler
// Any time the MCP2515 pings the interrupt pin of the 2560, indicating a message is ready in the CAN buffer, this is run
void ISR_can() {
  //Buffer variables are global.
  byte temp;
  lastISR = millis();

  canintf=CANRead(CANINTF); // Reading Interrupt to determine which buffer is full.

  if (canintf & B00000001) {
    SIDH=CANRead(RXB0SIDH);
    SIDL=CANRead(RXB0SIDL);
    EID8=CANRead(RXB0EID8);
    EID0=CANRead(RXB0EID0);
    DLC=CANRead(RXB0DLC);
    databuffer[0]=CANRead(RXB0D0);
    databuffer[1]=CANRead(RXB0D1);
    databuffer[2]=CANRead(RXB0D2);
    databuffer[3]=CANRead(RXB0D3);
    databuffer[4]=CANRead(RXB0D4);
    databuffer[5]=CANRead(RXB0D5);
    databuffer[6]=CANRead(RXB0D6);
    databuffer[7]=CANRead(RXB0D7);
  } 
  else if (canintf & B00000010) {
    SIDH=CANRead(RXB1SIDH);
    SIDL=CANRead(RXB1SIDL);
    EID8=CANRead(RXB1EID8);
    EID0=CANRead(RXB1EID0);
    DLC=CANRead(RXB0DLC);
    databuffer[0]=CANRead(RXB1D0);
    databuffer[1]=CANRead(RXB1D1);
    databuffer[2]=CANRead(RXB1D2);
    databuffer[3]=CANRead(RXB1D3);
    databuffer[4]=CANRead(RXB1D4);
    databuffer[5]=CANRead(RXB1D5);
    databuffer[6]=CANRead(RXB1D6);
    databuffer[7]=CANRead(RXB1D7);
  }

  block=((B01111000 & EID0) >> 3);
  temp=0x00;
  temp=((B00000100 & EID0) << 3);
  block=block | temp;

  offset=SIDH;
  temp=((SIDL & B11100000) >> 5);
  offset=((offset << 3) | temp);

  dataready = 1; // set flag to run parser in loop
  CANWrite(CANINTF, 0x00); // clear interrupt

  MS_Parse();
} // END ISR_can()


void MS_Parse() {
  dataready = 0;
  lastParse = millis();
  
  data=databuffer[0];
  data=((data << 8) | databuffer[1]);

  byte datalength=(DLC & 0x0F);

  byte temp;
  int var_offset;
  var_offset=SIDH;
  temp=((SIDL & B11100000) >> 5);
  var_offset=((var_offset << 3 )| temp);

  int msg_type;
  msg_type=((B00000011 & SIDL) << 1);
  temp=0x00;
  temp=((B10000000 & EID8) >> 7);
  msg_type=msg_type | temp;

  byte from_id, to_id;
  from_id=((B01111000 & EID8) >> 3);
  to_id=((B00000111 & EID8) << 1);
  temp=0x00;
  temp=((B10000000 & EID0) >> 7);
  to_id=to_id | temp;

  int var_block;
  var_block=((B01111000 & EID0) >> 3);
  temp=0x00;
  temp=((B00000100 & EID0) << 3);
  var_block=var_block | temp;

// Determine what data was received and update the associated (global) variable
// This code is, how you say... inelegant
  if(var_offset == 6){            // RPM
    canRPM = data;
  }else if(var_offset == 24){     // TPS
    canTPS = data;
  }else if(var_offset == 26){     // Battery Voltage
    canVoltage = String(((double)data)/10).substring(0,4);
  }else if(var_offset == 270){    // Gear
    canGear = databuffer[0];
  }else if(var_offset == 434){    // CEL Status(?)
    canCELStatus = data;
  }else if(var_offset == 226){    // TPSADC
    canTPSADC = data;
  }else if(var_offset == 22){     // CLT
    canCLT = data / 10;
  } 
//  if(var_offset == 106){   // Oil Pressure
//    canOLP = data / 10;
//  }
//  if(canCELErrorCode == 415){   // CEL Error Code
//    canCELErrorCode = databuffer[0];
//  }
  
  
  if(String(data).length() < 5){
    //showText(String(data));
  }else{
    showText(" . . .");
  }
} // End MS_Parse()


void CANWrite(byte addr, byte data) {
  digitalWrite(CS_PIN,LOW);
  noInterrupts(); // Necessary to avoid freezing during SPI transfer (due to MS_Parse and ISR_can both clearing the interrupt flag)
  SPI.transfer(CAN_WRITE);
  SPI.transfer(addr);
  SPI.transfer(data);
  interrupts();
  digitalWrite(CS_PIN,HIGH);
} // End CANWrite
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

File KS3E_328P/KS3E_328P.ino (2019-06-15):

//----------------------- UNO/328P
// KSU Motorsports/FSAE KS-2 Dashboard ATmega328P Firmware
// Clinton Flowers, 2017

#include <Wire.h>
#include <avr/wdt.h>

#include <Adafruit_NeoPixel.h> // Get this from the Arduino IDE Library Manager
#ifdef __AVR__
  #include <avr/power.h>
#endif

// Which pin on the Arduino is connected to the NeoPixels?
#define PIN            8

// How many NeoPixels are attached to the Arduino?
#define NUMPIXELS      20
#define numRows 2

Adafruit_NeoPixel pixels = Adafruit_NeoPixel(NUMPIXELS, PIN, NEO_GRB + NEO_KHZ800);

int delayval = 500; // delay for half a second
int8_t temp = 50;
int unoRpms = 0; // Local storage of engine RPM's
int megaAddress = 6;
int unoAddress = 5;
int ledArgs[7];

void setup() {
  wdt_enable(WDTO_120MS);
  pixels.begin(); // This initializes the NeoPixel library.
  Wire.begin(unoAddress); // Join the I2C bus
  Wire.setClock(400000L);
  Wire.onReceive(receiveRpmHandler);
} // End setup()

void loop() {
  wdt_reset();
  delay(1); // The latest code version is entirely based on I2C-initiated interrupts; see receiveRpmHandler
} // End loop()

void setPixelGroup(int beginPixels, int endPixels, int delayTime, int red, int green, int blue, int mode){
  // Multiple "modes" for different driver preferences on how the lights light up
  if(mode == 0){
   for(int i=beginPixels-1;i<endPixels;i++){
      // Light up each column of the lights, from left to right
      pixels.setPixelColor(i, pixels.Color(red,green,blue)); // Set top row
      pixels.setPixelColor((NUMPIXELS/(numRows-1))-1 - i, pixels.Color(red,green,blue)); // Set bottom row
      if(delayTime > 0){
        pixels.show(); // This sends the updated pixel color to the hardware.
        delay(delayTime); // Delay for a period of time (in milliseconds).
      }   
    } 
  }else if(mode == 1){
    for(int i=beginPixels-1;i<endPixels;i++){
      // Light up the columns of the shift lights, from left and right to center
      pixels.setPixelColor(i, pixels.Color(red,green,blue)); // Set top row left
      pixels.setPixelColor((NUMPIXELS/numRows)-1 - i, pixels.Color(red,green,blue)); // Set top row right
      pixels.setPixelColor((NUMPIXELS/(numRows-1))-1 - i, pixels.Color(red,green,blue)); // Set bottom row left
      pixels.setPixelColor(i + (NUMPIXELS/numRows), pixels.Color(red,green,blue)); // Set bottom row right
      if(delayTime > 0){
        pixels.show(); // This sends the updated pixel color to the hardware.
        delay(delayTime); // Delay for a period of time (in milliseconds).
      }
    }
  }
  pixels.show(); // This sends the updated pixel color to the hardware.
} // End setPixelGroup(int, int, int, int, int, int, int)

// Function that executes whenever data is received from the I2C master 2560 uC
// This function is registered as an event/ISR, see setup()
void receiveRpmHandler(int howMany) {
  for(int i = 0; i < sizeof(ledArgs); i++){
    ledArgs[i] = Wire.read();
  }
  pixels.clear();
  setPixelGroup(ledArgs[0], ledArgs[1], ledArgs[2], ledArgs[3], ledArgs[4], ledArgs[5], ledArgs[6]);
} // End receiveRpmHandler()

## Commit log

2017-07-01 Initial Commit
    Initial .SCH, .BRD, .PDF, Readme, and enclosure .STL's and .SLDPRT's
    [Dash Backplate.SLDPRT, Dash Faceplate.SLDPRT, Dash v0.2 Backplate - Formlabs Clear Resin.STL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]
2017-07-01 Attaching Image and License, fixing Readme
2018-03-21 Added code
    Added the current code for both microcontrollers
2018-03-21 Updating Footprint and Enclosure Model
    [Dash Faceplate Version 2.SLDPRT, Dash v0.2 Backplate Version 2.STL]
2018-04-03 Minor code fixes; Updated readme
    [Dash0.2_2560_Code.ino]

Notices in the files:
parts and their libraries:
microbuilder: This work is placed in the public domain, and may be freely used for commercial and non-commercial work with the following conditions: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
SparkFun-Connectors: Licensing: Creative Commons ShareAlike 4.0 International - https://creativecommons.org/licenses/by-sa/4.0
